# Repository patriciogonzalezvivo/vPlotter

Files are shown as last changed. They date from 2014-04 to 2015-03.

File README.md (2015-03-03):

### Basic principes 

The vPlotter is essentially a vertical drawing machine that consists of a marker suspended between two motors which moves it over a wall surface.

The math involved in the movement of the marker over the surface is extremely simple. It requires knowing the distance between the motors to calculate how much string distance each motor has to give to the marker (plotter head). This distance can be calculated using Pythagoras' theorem.

GRAPH

Both motors are attached to the wall at the same height to the floor separated by a given distance. The more distance there is between them, the larger the drawing area. I usually separate the motors by 1.5 meters (1500 mm). 

	distance_between_motors = 1500;

So the motors' positions can be represented as: 

	M1.x = 0;
	M1.y = 0;

	M2.x = M1.x + distance_between_motors;		// 1500
	M2.y = 0;

Knowing this we can calculate the position of the plotter head using Pythagoras' theorem. Imagine the triangles composed by the two motors and the plotter head as two right triangles. For each motor we need to find the distance (square root) to the marker. By releasing this amount of string to the plotter head, gravity will make the rest, by tensing the string.

	distance.M1 = square_root( M1.x*M1.x + M1.y*M1.y );
	distance.M2 = square_root( M2.x*M2.x + M2.y*M2.y );

To have precise control on the motors' movements, I'm using two [NEMA 17 steppers motors](https://ultimachine.com/content/kysan-1124090-nema-17-stepper-motor) controlled with a [Pololu A4988 Stepper Driver](https://ultimachine.com/content/pololu-a4988-stepper-driver-heatsink-kit) for each one. 

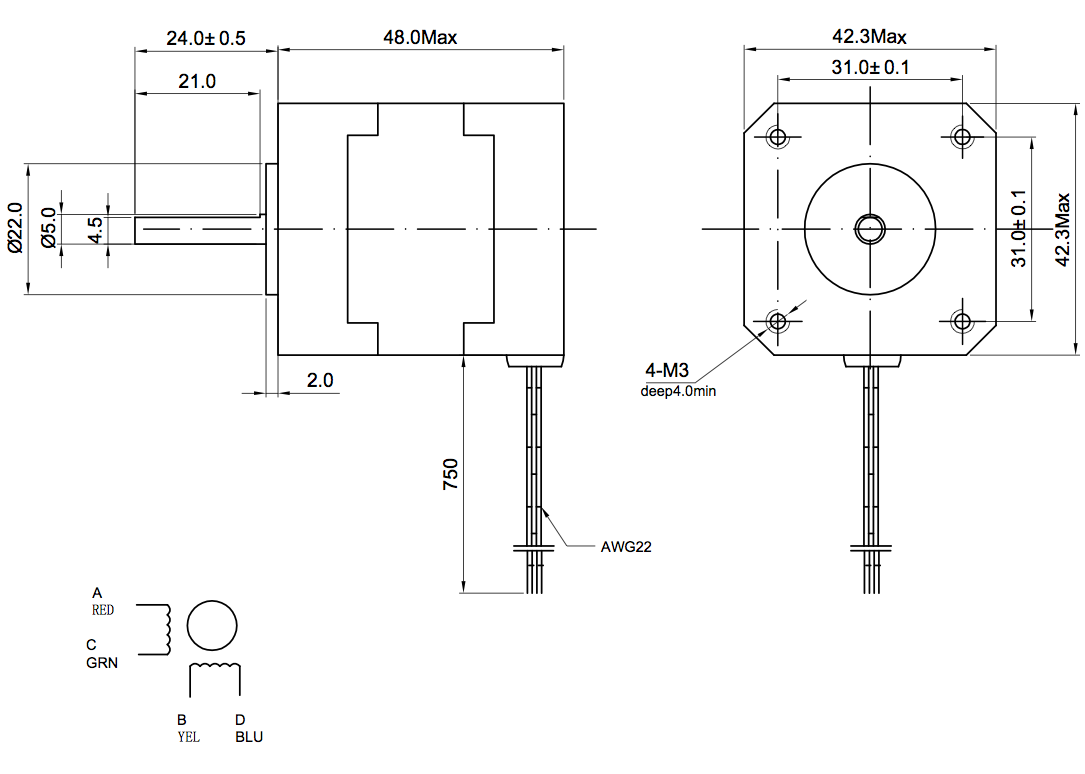
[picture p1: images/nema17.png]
nema17 (https://ultimachine.com/content/kysan-1124090-nema-17-stepper-motor)
 

Nema 17 motors have 200 steps for rotation but by enabling quarters of steps on the Pololu drivers we can obtain up to 800 steps for rotation which allows for much more precision. Next we need to calculate the circumference of the pulleys to determine how many millimeters we have for each step. In my case I'm using two [Timing Pulley GT2 of 20 tooth](https://ultimachine.com/content/timing-pulley-gt2-20-tooth) which have a bore of 5mm and match the [GT2 Timing Belt](https://ultimachine.com/content/timing-belt-gt2-custom-length) that holds the plotter header. From that we can calculate the amount of steps using these formulas:

	STEPS = 800;
	DIAMETER = 5; // 5mm
	CIRCUMFERENCE = DIAMETER * PI; // 15.7 mm
	m2s = CIRCUMFERENCE / STEPS; // 0.019625 mm for step

Keeping track of how much string each motor has moved we can estimate with a precision of 0.019625mm the position of the plotter head. I'm keeping track of the number of steps in a structured variable called MotorVal :

	struct MotorVal{
  	  long M1;
    	long M2;
	};

 To calculate the plotter drawing head we can use absolute parameters or relative. This means the an absolute position or a position relative to the previous one. In order to have accurate absolute positions is necessary to know the starting position of the plotting head. For that I use a physical mark on the center of the drawing area to manually adjust the plotter header at the beginning of each drawing work. Other drawing machines like laser cutters or CNC machines have sensors to estimate the initial position.

Another important feature of this drawing machine is the ability to start and stop drawing by moving the marker closer to or further from the wall surface. This is done using a [Micro Servo Motor](http://www.adafruit.com/products/169) mounted on the plotter head. Servos use frequency of pulse to calculate the angle of the motor. They can go from -90 to 90 deg (0 - 180 deg), alternating between 544 to 2400 pulses per second. By moving the marker towards or away from the surface, we can control when it is drawing lines and when it is just moving. This, together with the absolute or relative coordinates, defines 4 types of commands:

	enum Command{
  	  MOVE_ABS = 0,
    	MOVE_REL,
    	LINE_ABS,
    	LINE_REL
	};

Using these commands each line of a drawing is translated to instructions to the motors. 

	void vPlotter::print(vector<ofPolyline> _paths){
		for(int i = 0; i < _paths.size(); i++) {
			for(int j = 0; j < _paths[i].getVertices().size(); j++){
				addInstruction( ((j==0)?MOVE_ABS:LINE_ABS), _paths[i].getVertices()[j] );
			}
		}
		addInstruction(MOVE_ABS, printingArea.getCenter());
	}

	bool vPlotter::addInstruction(Command _command, ofPoint _pos){
		ofPoint t;

		//  ABSolute or RELative positions??
		//
		switch (_command) {
			case MOVE_ABS:
			case LINE_ABS:
				t = _pos;
				break;
			case MOVE_REL:
			case LINE_REL:
				t = _pos + currentPos;
				break;
		}

		//  Make instruction
		//
		Instruction inst;
		inst.set(_pos);
		inst.cmd = _command;
		inst.target = getStepsFor(_pos);

		//  Add
		//
		instructions.push_back(inst);
	}

	MotorVal vPlotter::getStepsFor(ofPoint _pos) {
		MotorVal val;
		val.M1 = M1.distance(_pos)/m2s;
		val.M2 = M2.distance(_pos)/m2s;
		return val;
	}

To ensure consistency, I'm adding an extra instruction that moves the head of the plotter to the center of the printing area. This prevents the user from having to manually move the head of the plotter to the physical mark on the center of the plotting area.

These instructions are then processed in another thread sending each motor the number of steps it has to move and in which direction. Controlling real motors means being constrained by real behavior - that means being aware of the physical stress (thermal and electrical) together with the time a task takes to be executed. This is the function that executes the instructions, that calculates the pauses and pulses to the motors. 

	void vPlotter::threadedFunction(){
		while( isThreadRunning() != 0 ){
			if (isPrinting()){
				if(getInstructionsLeft()){
					if (exeInstruction(instructions[0])){
						if(lock()){
							instructions.erase(instructions.begin());
							unlock();
						}
					}
				} else {
					bPlotting = false;
					stopThread();
				}
			}
		}
	}

	bool vPlotter::exeInstruction(Instruction _inst){
		MotorVal t, s;
		float sd,pd;

		//  Set the right PEN
		//
		sd = stepDelay*1000.0f;
		pd = penDelay*1000.0f;
		switch (_inst.cmd) {
			case LINE_REL:
			case LINE_ABS:{
				if(penState == PEN_UP){
					softServoWrite(SERVO_PIN,penPosDown);
					usleep(pd);
				}
				penState = PEN_DOWN;
				break;
			}
			case MOVE_REL:
			case MOVE_ABS:{
				if(penState == PEN_DOWN){
					softServoWrite(SERVO_PIN,penPosUp);
					usleep(pd);
				}
				penState = PEN_UP;
				break;
			}
		}

		// Tmp Variables
		t = target = _inst.target;
		s = steps;
    
		// set directions
		MotorVal dir;
		dir.M1 = (t.M1 > s.M1) ? +1 : -1;
		dir.M2 = (t.M2 > s.M2) ? +1 : -1;
		digitalWrite(DIR_PIN_M1, (t.M1 > s.M1) ? DIR_UP : DIR_DOWN);
		digitalWrite(DIR_PIN_M2, (t.M2 > s.M2) ? DIR_DOWN : DIR_UP);

		//  Make steps
		//
		while (s!=t){
			if( t.M1 - s.M1 != 0){
				digitalWrite(STEP_PIN_M1, HIGH);
				s.M1 += dir.M1;
			}

			if(t.M2-s.M2 != 0){
				digitalWrite(STEP_PIN_M2, HIGH);
				s.M2 += dir.M2;
			}

			steps = s;
			currentPos = getPosFor(s);
			usleep(250);
			digitalWrite(STEP_PIN_M1, LOW);
			digitalWrite(STEP_PIN_M2, LOW);
			usleep(250);
			usleep(sd);
		}
		return true;
	}

	//	Reverse kinematics
	//
	ofPoint vPlotter::getPosFor(MotorVal _steps) {
		float a = _steps.M2 * m2s;
		float b = _steps.M1 * m2s;
		float c = motorsDistance;
		return calcPointB(a, b, c);
	}

	ofPoint vPlotter::calcPointB(float a, float b, float c){
		double angle = acos((b*b+c*c-a*a)/(2*b*c));
		return ofPoint(b*cos(angle)+M1.x,b*sin(angle)+M1.y);
	}

These functions are the core operations behind the drawing. To make the vPlotter a proper tool I designed a reliable and flexible infrastructure based on openFrameworks (C++) and Node (JS) on top of a Linux OS running on a raspberryPi.

### Hardware

- 2 x [Nema 17 Stepper Motor](https://ultimachine.com/content/kysan-1124090-nema-17-stepper-motor)

- 2 x [Pololu A4988 Stepper Driver](https://ultimachine.com/content/pololu-a4988-stepper-driver-heatsink-kit)

- 2 x [Timing Pulley, GT2, 20 Tooth](https://ultimachine.com/content/timing-pulley-gt2-20-tooth)

- 6m of [Timing Belt, GT2, Custom Length](https://ultimachine.com/content/timing-belt-gt2-custom-length)

- 1 x [Micro Servo](http://www.adafruit.com/products/169) 

- 15x15 inch of Plywood 

- [Raspberry Pi](https://www.adafruit.com/products/998)

- [GPIO Ribbon Cable](https://www.adafruit.com/products/862)

- [Adafruit Half-size Perma-Proto](https://www.adafruit.com/products/1148)

- Optional [PiTFT](https://www.adafruit.com/products/1601) screen for visual debug

RaspberryPi is a small and cheap board capable of running a complete Linux system. The RaspberryPi has some General Input's and Outputs (GPIO) that will let us connect this board to the stepper motors' drivers (Pololu) and the mini servo motors.

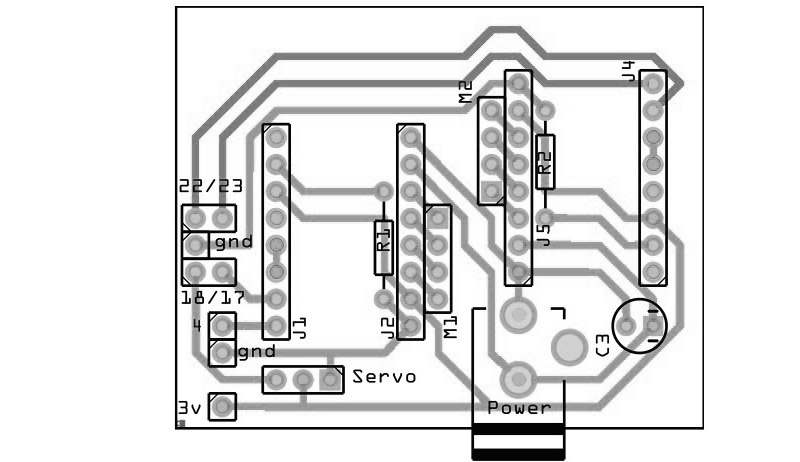
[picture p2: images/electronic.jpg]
Electronic Board


Because the servo uses frequency of pulses it will use the GPIO number 18 that has PWM capabilities. For the two motor drivers we use the GPIOs 4, 17, 23 and 22. Each driver will require both a _step_ and a _direction_ pulse to know when and how to make the rotation. These values can be modified at the top of the `vPlotter.h` file

	#define SERVO_PIN 18

	#define STEP_PIN_M1 4
	#define DIR_PIN_M1 17

	#define STEP_PIN_M2 23
	#define DIR_PIN_M2 22

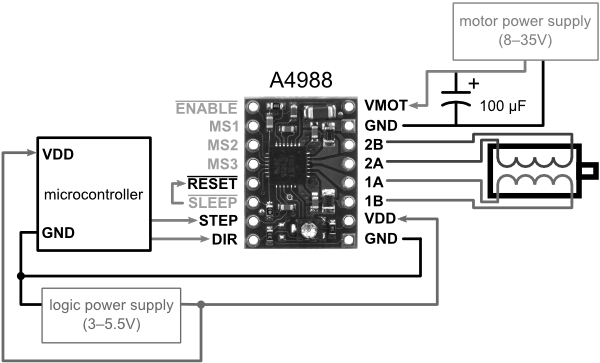
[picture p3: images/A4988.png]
A4988


### Software

The RaspberryPi uses a derived version of the Debian Linux distribution as its operating system. This software architecture is famous for it stability, security and modularity. Each new program installed onto the computer becomes part of a robust ecosystem of applications that can be re-combined in different ways.

In the case of the vPlotter the C++ code I wrote using openFrameworks constitutes the core application capable of being executed directly from the command line as follows:

	vPlotter -i file.svg

It is possible to modify some setup parameters like the distance between motors by doing:

	vPlotter -d 2000 -i file.svg

This application can print vector files (known as SVG format) and can also listen for instructions on a OSC port (for example the port 1010101).

	vPlotter -o 101010

Another feature of this application is the possibility of receiving visual feedback of the instructions on the pull by adding the option -x

	vPlotter -x -o 1010101
	vPlotter -x -i file.svg

It's possible to combine vPlotter with other tools using Unix pipe commands like this: 

	potrace -s image.png || vPlotter -i

In this case we are using the program ['potrace'](http://potrace.sourceforge.net/) to transform an image to vectors (-s) to then print it using vPlotter. Using similar techniques, it is possible to transform a picture of a document to text to then assign some style and fonts to then vectorize and finally print with the plotter. The combinations are infinite.

But not all users are comfortable running linux commands as part of their creative practice. That's why I design a Node.js server that provides an web API to administrate calls to the vPlotter. Users can ask for jobs in the plotter queue together with the setup parameters by making a call to `rpi.local:8080/status.json`. Using the same API users can `add` tasks to the queue or change the setting options of the vPlotter. A hypothetical user with intermediate knowledge of HTML/CSS/JS can use the plotter remotely by sending and receiving calls to this API.

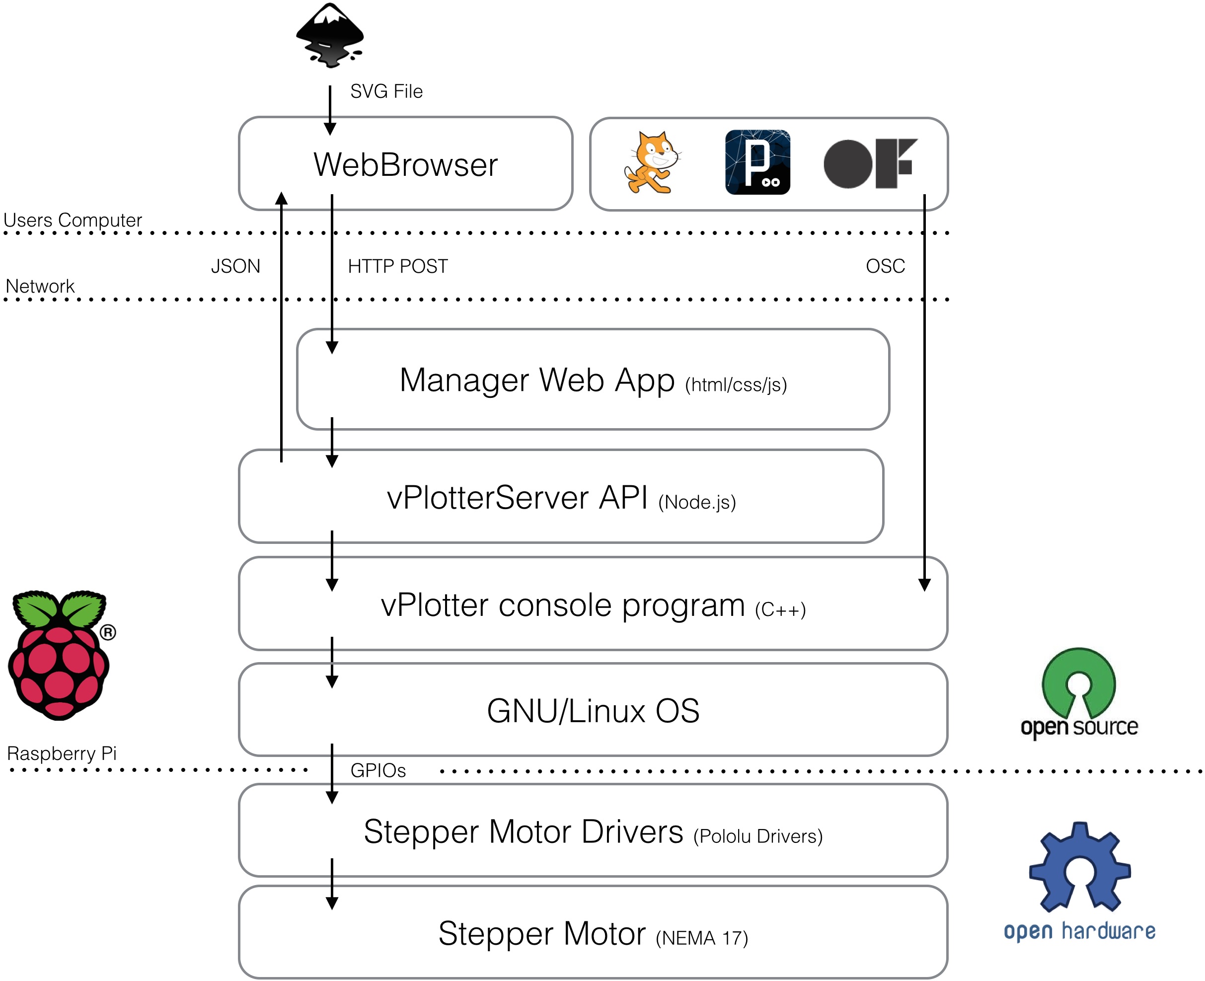
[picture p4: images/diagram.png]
Modular design of the vPlotter


It's possible that the user does not have the technical knowledge to use the API, which is why I have also incorporated on the server a web site from which it is possible to drag & drop files to the queue. I've designed a tool that can be access ed from a wide spectrum of architectural layers.

<iframe src="//player.vimeo.com/video/81298249?title=0&amp;byline=0&amp;portrait=0&amp;color=ffffff" width="574" height="323" frameborder="0" webkitallowfullscreen mozallowfullscreen allowfullscreen></iframe>

##### Software Installation

1. In order to compile and install the vPlotter binaries in the right place you will need to [install openFrameworks](http://openframeworks.cc/setup/raspberrypi/Raspberry-Pi-Getting-Started.html). For that please follow [this guide](http://openframeworks.cc/setup/raspberrypi/Raspberry-Pi-Getting-Started.html). Be prepared, it is going to take a while.

2. Once you have your openFrameworks installed and working (please check it by compiling some of the examples), clone this repository inside the `/home/pi/openframeworks/apps` folder.

~~~
	cd ~/openFrameworks/apps
	git clone https://github.com/patriciogonzalezvivo/vPlotter
~~~

5. The last step is to run the installation script which will install [Node.js](http://nodejs.org/) for the server, [WiringPi](https://projects.drogon.net/raspberry-pi/wiringpi/) to communicate through the GPIOs, compile `vPlotter` and install `vPlotterServer` as a local daemon.

~~~
	cd ~/openFrameworks/apps/vPlotter
	./install.sh
~~~

### Precedents & Research

Wall Plotter has been around for a while. My work is continuing what others have started. The first documented wall-plotter was develop by [Jurg Lehni]((http://juerglehni.com), and was called [Hektor](http://juerglehni.com/works/hektor/). Jurg is a fascinating artist committed to tool making, especially related to drawing.

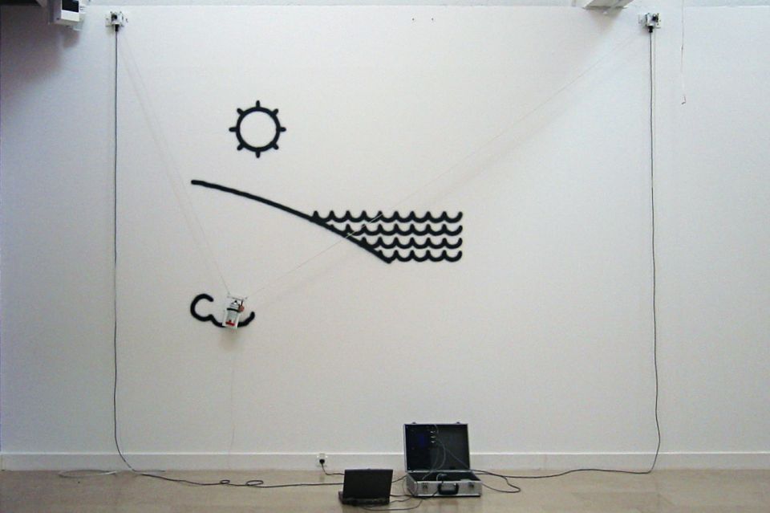
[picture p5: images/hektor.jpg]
Hektor by Jurg Lehni (http://juerglehni.com/works/hektor/)


In my case I start working based on [Alexander Weber's](http://tinkerlog.com/) wall plotter called [Kritzler](http://tinkerlog.com/2011/09/02/der-kritzler/). He's done amazing work documenting the process together with comprenhensible [code](https://github.com/tinkerlog/Kritzler). This version is designed to run with an Arduino plugged into a computer. My first effort on this project was porting the code to openFrameworks to then compile and run on the RaspberryPi, but the basic core logics behind the algorithmic kinematics are pretty much the same as what Alex wrote.

Kritzler by Alexander Weber (http://tinkerlog.com/2011/09/02/der-kritzler/)

Alexander documentation (http://tinkerlog.com/2011/09/02/der-kritzler/)

While I was experimenting with the Plotter I rapidly discovered how important it is to calculate the right printing area. The variations on the tensions on the strings that hold the plotter head are vital to obtain good results on the marker traces.

Doing some research I found some valuable documentation on [this website](http://2e5.com/plotter/V/design/) of how to obtain both resolution and tension coefficient. Since they are presented in Python I translated them into C++ and added to some methods and functions that calculate the best area given a specific distance between the motors.

Printing Area (http://2e5.com/plotter/V/design/)

The presence of mathematics concepts in drawings have a long history. The laws of perspective and proportions are one of the first technical tools we use. In my process of making a drawing machine I learned how to connect and work together with physics and mechanical principles. 

Sometimes drawing tools aren't born from a long history of techniques and apparatus. They are discovered as the repurpose of everyday machines. This is the case of the drawings made by [Echo Yang](http://www.junk-culture.com/2014/02/designer-transforms-old-school-analog.html#more).

Echo Yang's drawing machine (http://www.junk-culture.com/2014/02/designer-transforms-old-school-analog.html#more)

There are other examples of drawing machines, ones that formulate a question not about the tools but about the user. These are the cases of sophisticated robots armed with regular brushes and analog paint. These robots mimic our use of these tools in the search of becoming autonomous agents. [eDavid](http://www.informatik.uni-konstanz.de/en/edavid/news/) designed by Oliver Deussen and Thomas Lindemeier is an example of a machine that performs accurate drawings, while the robot designed by [Benjamin Grosser](http://bengrosser.com/projects/interactive-robotic-painting-machine/) explores some "expressive" visual representations of sound.

Ben Grosser Drawing Machine (http://bengrosser.com/projects/interactive-robotic-painting-machine/)

##### More references to drawing machines

- [Viktor](http://www.we-find-wildness.com/2011/01/juerg-lehni-viktor/)

- [Norwegian Creation's Drawing Machine](http://www.norwegiancreations.com/2012/04/drawing-machine-part-2/)

- [SADbot](http://www.instructables.com/id/SADbot-the-Seasonally-Affected-Drawing-robot/)

- [Harvey Moon's The Drawing Machine](http://www.unanything.com/Drawbot.html)

- <http://www.kickstarter.com/projects/notever/the-drawing-machine > <http://www.creativeapplications.net/maxmsp/drawing-machine-maxmsp-processing/>

- [Der Kritzler](http://tinkerlog.com/2011/09/02/der-kritzler/
Polargraph )

- <http://www.polargraph.co.uk>

- [Tristan Perich's Drawing Machine](http://tristanperich.com/Art/Machine_Drawings/)

- Paul Ferragut's Wall Drawing Machine: <http://vimeo.com/20526787> <http://vimeo.com/35647507> <http://vimeo.com/26900180>

- Douglas Irving Repetto's Giant Painting Machine:<http://music.columbia.edu/~douglas/portfolio/GPM_sanmateo_peoria_sf/> <http://music.columbia.edu/~douglas/portfolio/GPM_milano/>

- [Sprite Mod's White Board Plotter](http://spritesmods.com/?art=whiteboard&f=had)

- DrawBot:<http://www.marginallyclever.com/category/drawbot-my-creations/> <https://github.com/i-make-robots/DrawBot>
<http://web.me.com/sami6877/unanything/Site/Secret_Work/Entries/2010/6/1_Drawbot.html> <http://blog.makezine.com/2010/07/30/drawbot-takes-its-time-to-sketch/>

- [AS220 Lab's Drawbot](http://www.as220.org/labs/drawbot/instructions.html)

- [Make Magazine's Drawing Machine](http://makezine.com/makeitlast/) <http://makermedia.cmail4.com/t/ViewEmail/r/351C80A070878603/6423113868B805CEC9C291422E3DE149>
<http://blog.makezine.com/2011/02/24/make-it-last-build-3-rigging-up-your-drawbot/>

- [Muralizer](http://www.muralizer.com/blog/) <http://www.kickstarter.com/projects/1910641777/muralizer-it-prints-on-walls> <http://blog.makezine.com/2009/10/29/muralizer-prints-art-on-the-wall/> 

- [InternBot](http://jamesprovost.com/blog/introducing-internbot/)

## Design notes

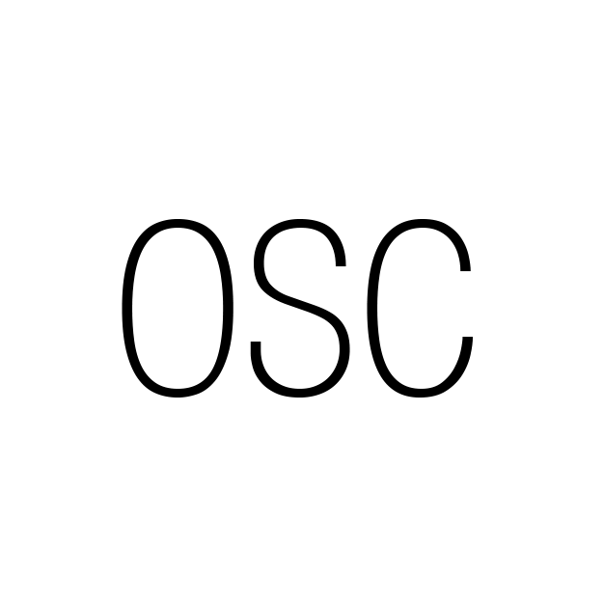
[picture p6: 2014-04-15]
vPlotterServer/www/images/osc.png

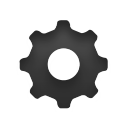
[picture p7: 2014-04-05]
vPlotterServer/www/images/gear.png

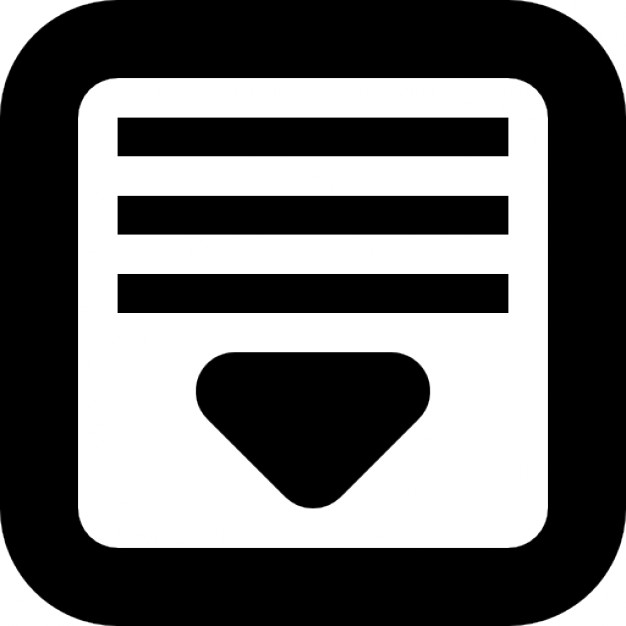
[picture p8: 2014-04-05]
vPlotterServer/www/images/main.jpg

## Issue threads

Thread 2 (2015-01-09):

Erroe while trying to Make vPlotter

LangBalthazar, 2015-01-09:
Hi,

Your project seems great! And I would very much like to try your setup.

But when i try to make according to your installation guide it fails as below on:
```
fatal error: ofxPiTFT.h: Filen eller katalogen finns inte
compilation terminated.
```
translated to ofxPiTFT.h is missing.

It is included online 6 and 27 in vPlotter/vPlotter/src/ofApp.h
If i comment out both refs to ofxPiTFT in ofApp.h it makes (with only warnings on other things)

The full make process below:
```
pi@drinkpi ~/openFrameworks/apps/vPlotter/vPlotter $ make
armv6l
checking pkg-config libraries:   cairo zlib gstreamer-app-1.0 gstreamer-1.0 gstreamer-video-1.0 gstreamer-base-1.0 libudev freetype2 fontconfig sndfile openal openssl libpulse-simple alsa gtk+-2.0 libmpg123
Compiling OF library for Release
armv6l
checking pkg-config libraries:   cairo zlib gstreamer-app-1.0 gstreamer-1.0 gstreamer-video-1.0 gstreamer-base-1.0 libudev freetype2 fontconfig sndfile openal openssl libpulse-simple alsa gtk+-2.0 libmpg123
make[1]: Entering directory `/home/pi/openFrameworks/libs/openFrameworksCompiled/project'
armv6l
checking pkg-config libraries:   cairo zlib gstreamer-app-1.0 gstreamer-1.0 gstreamer-video-1.0 gstreamer-base-1.0 libudev freetype2 fontconfig sndfile openal openssl libpulse-simple alsa gtk+-2.0 libmpg123
make[2]: Inget behöver göras för "ReleaseABI".
armv6l
checking pkg-config libraries:   cairo zlib gstreamer-app-1.0 gstreamer-1.0 gstreamer-video-1.0 gstreamer-base-1.0 libudev freetype2 fontconfig sndfile openal openssl libpulse-simple alsa gtk+-2.0 libmpg123
Done!
make[1]: Leaving directory `/home/pi/openFrameworks/libs/openFrameworksCompiled/project'

Compiling vPlotter for Release
armv6l
checking pkg-config libraries:   cairo zlib gstreamer-app-1.0 gstreamer-1.0 gstreamer-video-1.0 gstreamer-base-1.0 libudev freetype2 fontconfig sndfile openal openssl libpulse-simple alsa gtk+-2.0 libmpg123
make[1]: Entering directory `/home/pi/openFrameworks/apps/vPlotter/vPlotter'
../../../libs/openFrameworksCompiled/project/makefileCommon/config.project.mk:179: The following unknown addons will be ignored:
../../../libs/openFrameworksCompiled/project/makefileCommon/config.project.mk:180: ofxPiTFT
Compiling src/main.cpp
g++ -c -O3 -Wall -march=armv6 -mfpu=vfp -mfloat-abi=hard -fPIC -ftree-vectorize -Wno-psabi -pipe -DOF_USING_GTK -DOF_USING_MPG123 -DTARGET_RASPBERRY_PI -DSTANDALONE -DPIC -D_REENTRANT -D_LARGEFILE64_SOURCE -D_FILE_OFFSET_BITS=64 -D_FORTIFY_SOURCE -D__STDC_CONSTANT_MACROS -D__STDC_LIMIT_MACROS -DTARGET_POSIX -DHAVE_LIBOPENMAX=2 -DOMX -DOMX_SKIP64BIT -DUSE_EXTERNAL_OMX -DHAVE_LIBBCM_HOST -DUSE_EXTERNAL_LIBBCM_HOST -DUSE_VCHIQ_ARM -DUSE_DISPMANX_TRANSFORM_T -I./addons/ofxWiringPi/libs/wiringPi/include -I./vPlotter.xcodeproj/xcshareddata -I./vPlotter.xcodeproj/xcshareddata/xcschemes -I./src -I./addons -I./addons/ofxWiringPi -I./addons/ofxWiringPi/libs -I./addons/ofxWiringPi/libs/wiringPi -I./addons/ofxWiringPi/libs/wiringPi/libs -I./addons/ofxWiringPi/libs/wiringPi/include -I../../../addons/ofxOsc/src -I../../../addons/ofxOsc/libs -I../../../addons/ofxOsc/libs/oscpack -I../../../addons/ofxOsc/libs/oscpack/src -I../../../addons/ofxOsc/libs/oscpack/src/osc -I../../../addons/ofxOsc/libs/oscpack/src/ip -I../../../addons/ofxOsc/libs/oscpack/src/ip/posix -I../../../addons/ofxOsc/libs/oscpack/src/ip/win32 -I../../../addons/ofxSvg/src -I../../../addons/ofxSvg/libs -I../../../addons/ofxSvg/libs/svgTiny -I../../../addons/ofxSvg/libs/svgTiny/src -I/opt/vc/include -I/opt/vc/include/IL -I/opt/vc/include/interface/vcos/pthreads -I/opt/vc/include/interface/vmcs_host/linux -pthread -D_REENTRANT -I/usr/include/cairo -I/usr/include/glib-2.0 -I/usr/lib/arm-linux-gnueabihf/glib-2.0/include -I/usr/include/pixman-1 -I/usr/include/freetype2 -I/usr/include/libpng12 -I/usr/include/gstreamer-1.0 -I/usr/include/alsa -I/usr/include/gtk-2.0 -I/usr/lib/arm-linux-gnueabihf/gtk-2.0/include -I/usr/include/atk-1.0 -I/usr/include/gdk-pixbuf-2.0 -I/usr/include/pango-1.0 -I/usr/include/gio-unix-2.0/ -I/usr/include/harfbuzz -I../../../libs/fmodex/include -I../../../libs/glfw/include -I../../../libs/glfw/include/GLFW -I../../../libs/kiss/include -I../../../libs/openssl/include -I../../../libs/openssl/include/openssl -I../../../libs/poco/include -I../../../libs/rtAudio/include -I../../../libs/tess2/include -I../../../libs/openFrameworks -I../../../libs/openFrameworks/events -I../../../libs/openFrameworks/app -I../../../libs/openFrameworks/graphics -I../../../libs/openFrameworks/video -I../../../libs/openFrameworks/sound -I../../../libs/openFrameworks/types -I../../../libs/openFrameworks/gl -I../../../libs/openFrameworks/communication -I../../../libs/openFrameworks/utils -I../../../libs/openFrameworks/3d -I../../../libs/openFrameworks/math  -MMD -MP -MF obj/linuxarmv6l/Release/src/main.d -MT obj/linuxarmv6l/Release/src/main.o -o obj/linuxarmv6l/Release/src/main.o -c src/main.cpp
In file included from src/main.cpp:3:0:
src/ofApp.h:6:22: fatal error: ofxPiTFT.h: Filen eller katalogen finns inte
compilation terminated.
make[1]: *** [obj/linuxarmv6l/Release/src/main.o] Fel 1
make[1]: Leaving directory `/home/pi/openFrameworks/apps/vPlotter/vPlotter'
make: *** [Release] Fel 2
pi@drinkpi ~/openFrameworks/apps/vPlotter/vPlotter $
```

patriciogonzalezvivo, 2015-01-09:
Sorry, I forget to add a line on the documentation to clone the addon [ofxPiTFT](https://github.com/patriciogonzalezvivo/ofxPiTFT)

Closed 2015-01-09.

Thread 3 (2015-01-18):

Servo gitter

LangBalthazar, 2015-01-18:
Thank you for all your work. I have a question related to the servo.

I have everything wired up and workin on my desk but the servi is very jumpy.

It has the power to lift my heavy gondola with two 6005 bearings but it is jumping all the time
See example here:
http://www.youtube.com/watch?v=vTT_pI-Varo

I sit just me or is the normal behavior?

If I putty in and do a mode switch to pwm the servo is silent and then sudo gpio pwm 1 122 it moves and then silent.
Once I export the port again as done in the file in vplotterserver it starts to jump and make noise as in the video.

Is this Normal or do you any hints on how to improve this?

LangBalthazar, 2015-01-18:
In the video I have the servo connected to gpio18 / wiringpi gpio1, 3.3v and gnd on the pi The idle movements and noise is much louder when running servo + on 5v from the pi

patriciogonzalezvivo, 2015-01-23:
Hi @LangBalthazar ! yes I was having similar behavior. but stops once the GPIO library was load with the program. That's probably because of the noise on the GPIOs and the way servos works. There should be a way to fix it with proper wiring, but I don't know how to do it yet. Let me know if you find any tip. Thanks

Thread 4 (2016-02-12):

lines = p.getOutline  initialization of reference of type error

elid, 2016-02-12:
Hi Patricio,
First Thanks for your amazing work on the vPlotter :)
I had to correct the line 29 on ofApp.cpp file to compile the app correctly
from
vector<ofPolyline>& lines = p.getOutline();
to
vector<ofPolyline>& lines = const_cast<vector<ofPolyline>&>(p.getOutline());
apparently p.getOutline need to cast as a polyline array on raspberry pi

Since I'm quite new to oF and to c++, I could not figure out how to use your UI version yet,
but I'll dig a bit deeper and will surely find out.

Thanks!
/Frederic

sobrien556, 2019-03-26:
Hi Frederic, I am still receiving an error upon compilation, even with your suggestions. I have attached the screenshot of the errors I recieved. Thanks!
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
(url)

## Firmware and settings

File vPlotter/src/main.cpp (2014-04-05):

#include "ofMain.h"

#include "ofApp.h"
#include "ofAppNoWindow.h"

#include <algorithm>

char* getCmdOption(char ** begin, char ** end, const std::string & option){
    char ** itr = std::find(begin, end, option);
    if (itr != end && ++itr != end)
    {
        return *itr;
    }
    return 0;
}

bool cmdOptionExists(char** begin, char** end, const std::string& option){
    return std::find(begin, end, option) != end;
}

void printVersion(){
    cout << "vPlotter 0.1" << endl;
    cout << "Copyright (c) 2013 Patricio Gonzalez Vivo ( http://www.patriciogonzalezvivo.com )" << endl;
    cout << "This is free software with ABSOLUTELY NO WARRANTY." << endl;
}

//========================================================================
int main(int argc, char * argv[]){
    
    //  SYSTEM
    //----------------------------------------------
    //
#ifdef TARGET_RASPBERRY_PI
    bool noWindows = true;
    if(cmdOptionExists(argv, argv+argc, "-x")){
        noWindows = false;
    }
#else
    bool noWindows = false;
#endif
    ofAppNoWindow noWindowApp;
    if(noWindows){
        ofSetupOpenGL(&noWindowApp, 1024,768, OF_WINDOW);
    } else {
        ofSetupOpenGL(1024,768, OF_WINDOW);
    }
    
    ofApp *app = new ofApp();
    app->sysGpio = true;
    app->bFit = true;
    app->file = "tux.svg";
    app->scale = 100;
    app->rotate = 0;
    app->mmMotorsDistance = 1500;
    app->mmPulleyRadius = 5;
    app->stepsPerRotation = 800;
    app->stepDelay = 1;
    app->degPenUp = 140;
    app->degPenDown = 70;
    app->penDelay = 2000;
    app->oscPort = -1;
    
    if(cmdOptionExists(argv, argv+argc, "-gipo")){
        app->sysGpio = false;
    }
    
    //  HELP
    //
    if(cmdOptionExists(argv, argv+argc, "-v")){
        printVersion();
        return 0;
    }
    
    if(cmdOptionExists(argv, argv+argc, "-h")){
        printVersion();
        cout << endl;
        cout << "Usage: vPlotter [options] -i file.svg" << endl;
        cout << endl;
        cout << "Options:" << endl;
        cout << "   -s [0-100]  Scale the image. Default: " << app->scale << endl;
        cout << "   -r [deg]    Rotate the image. Default: " << app->rotate << endl;
        cout << "   -nf         Don't fit." << endl;
        cout << "   -d [mm]     Distance between motors in mm. Default: " << app->mmMotorsDistance << endl;
        cout << "   -pr [mm]    Pulley Radius in mm. Default: " << app->mmPulleyRadius << endl;
        cout << "   -spr [stp]  Steps per Rotation. Default: " << app->stepsPerRotation << endl;
        cout << "   -sd [ms]    Step Delay. Default: " << app->stepDelay << endl;
        cout << "   -pu [deg]   Pen Up Angle. Default: " << app->degPenUp << endl;
        cout << "   -pd [deg]   Pen Down Angle. Default: " << app->degPenDown << endl;
        cout << "   -delay [ms] Pen Delay. Default: " << app->penDelay << endl;
        cout << "   -gipo       Direct GPIO connection. Not throught /dev/ files. Require Root priviledge" << endl;
        cout << "   -x          X Debug Windows. Default: "<< noWindows << endl;
        cout << "   -o [port]   Stream mode to OSC Port" << endl;
        return 0;
    }
    
    //  INPUT SVG file
    //
    char * filename = getCmdOption(argv, argv+argc, "-i");
    char * oscPort = getCmdOption(argv, argv+argc, "-o");

    if (filename){
        app->file = filename;
    }
    else if(oscPort){
        app->oscPort = ofToInt(oscPort);
    }
#ifdef TARGET_RASPBERRY_PI
    else {
        cout << "Usage: vPlotter [options] -i file.svg" << endl;
        return 0;
    }
#endif
    
    if(cmdOptionExists(argv, argv+argc, "-nf")){
        app->bFit = false;
    }
    
    char * scale = getCmdOption(argv, argv+argc, "-s");
    if(scale){
        app->scale = ofToFloat(scale);
    }
    
    char * rotate = getCmdOption(argv, argv+argc, "-r");
    if(rotate){
        app->rotate = ofToFloat(rotate);
    }
    
    //  MOTORS
    //
    char * d = getCmdOption(argv, argv+argc, "-d");
    if(d){
        app->mmMotorsDistance = ofToInt(d);
    }
    
    char * pr = getCmdOption(argv, argv+argc, "-pr");
    if(pr){
        app->mmPulleyRadius = ofToInt(pr);
    }

    char * spr = getCmdOption(argv, argv+argc, "-spr");
    if(spr){
        app->stepsPerRotation = ofToInt(spr);
    }
    
    char * sd = getCmdOption(argv, argv+argc, "-sd");
    if(sd){
        app->stepDelay = ofToFloat(sd);
    }
    
    //  PEN
    //
    char * pu = getCmdOption(argv, argv+argc, "-pu");
    if(pu){
        app->degPenUp = ofToInt(pu);
    }
    
    char * pd = getCmdOption(argv, argv+argc, "-pd");
    if(pd){
        app->degPenDown = ofToInt(pd);
    }
    
    char * pdelay = getCmdOption(argv, argv+argc, "-delay");
    if(pdelay){
        app->penDelay = ofToFloat(pdelay);
    }

    ofRunApp( app );
}

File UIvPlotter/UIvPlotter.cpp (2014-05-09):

//
//  UIvPlotter.cpp
//  09 - TraceMaker
//
//  Created by Patricio Gonzalez Vivo on 10/9/13.
//
//

#include "UIvPlotter.h"

UIvPlotter::UIvPlotter(){
    motorsDistance      = 500;//1549;
    pulleyRadius        = 5;
    stepsPerRotation    = 800;
    
    host                = "192.168.1.12";
    oscPort             = 101010;

    currentPos.set(0,0);
    
    steps.M1    = 0;
    steps.M2    = 0;
    
    target.M1   = 0;
    target.M2   = 0;
    
    penState    = PEN_UP;
    bPlotting   = false;
    
    checkHostValues();
    sender.setup(host, oscPort);
    
//    textField = NULL;
}

void UIvPlotter::setupUI(){
//    textField = gui->addTextInput("HOST", "", OFX_UI_FONT_SMALL);
    
    gui->addLabel("Config");
    gui->addIntSlider("motorsDistance_(mm)", 0, 2000, &motorsDistance);
    gui->addIntSlider("pulleyRadius_(mm)", 0, 50, &pulleyRadius);
    gui->addIntSlider("stepsPerRotation", 0, 1000, &stepsPerRotation);
    gui->addIntSlider("penUp_(deg)", 0, 180, &penUp);
    gui->addIntSlider("penDown_(deg)", 0, 180, &penDown);
    bool bFalse = false;
    gui->addButton("SYNC", bFalse);
    
    gui->addButton("CLOSE", bFalse);
}

void UIvPlotter::guiEvent(ofxUIEventArgs &e){
    string name = e.widget->getName();
    
    if (name == "HOST"){
//        host = textField->getTextString();
        checkHostValues();
    } else if(name == "SYNC"){
        checkHostValues();
    } else if(name == "CLOSE"){
        ofxOscMessage m;
        m.setAddress("/stop");
        sender.sendMessage(m);
    } else {
        bUpdate = true;
    }
}

bool UIvPlotter::checkHostValues(){
    ofxJSONElement  response;
    
    std::string url = "http://"+host+":8080/status.json";
    
	if (!response.open(url)){
        cout  << "Failed to parse JSON\n" << endl;
    }
    
    penUp = ofToInt(response["options"]["penUpAngle"].asString());
    penDown = ofToInt(response["options"]["penDownAngle"].asString());
    motorsDistance = ofToInt(response["options"]["motorsDistance"].asString());
    pulleyRadius = ofToInt(response["options"]["pulleyRadius"].asString());
    stepsPerRotation = ofToInt(response["options"]["stepsPerRotation"].asString());
    
    bUpdate = true;
}

bool UIvPlotter::isHealthyAt(ofPoint _pos){
    ofVec2f tension = getTension(_pos);
    ofVec2f resolution = getResolution(_pos);
    if(tension.x<0||tension.y<0||
       tension.x>=0.8||tension.y>=0.8||
       resolution.x>=0.8||resolution.y>=0.8){
        return false;
    } else {
        return true;
    }
}

MotorVal UIvPlotter::getStepsFor(const ofPoint &_pos)const{
    MotorVal rta;
    rta.M1 = M1.distance(_pos)/m2s;
    rta.M2 = M2.distance(_pos)/m2s;
    return rta;
}

ofPoint UIvPlotter::getPosFor(const MotorVal &_steps)const{
    ofPoint rta;
    float a = _steps.M2 * m2s;
    float b = _steps.M1 * m2s;
    float c = motorsDistance;
    return calcPointB(a, b, c);
}

ofVec2f UIvPlotter::getTension(ofPoint _pos){
    float angleToM1 = atan2(_pos.y-M1.y,_pos.x-M1.x);
    float angleToM2 = atan2(_pos.y-M2.y,M2.x-_pos.x);
    float d = cos(angleToM1)*sin(angleToM2)+sin(angleToM1)*cos(angleToM2);
    float tensionToM1 = cos(angleToM2)/d;
    float tensionToM2 = cos(angleToM1)/d;
    return ofVec2f(tensionToM1,tensionToM2)-ofVec2f(0.5,0.5);
}

ofPoint UIvPlotter::calcPointB(float a, float b, float c)const{
    // law of cosines
    // http://en.wikipedia.org/wiki/Solution_of_triangles
    float angle = acos((b*b+c*c-a*a)/(2*b*c));
    return ofPoint(b*cos(angle)+M1.x,b*sin(angle)+M1.y);
}

ofVec2f UIvPlotter::getResolution(ofPoint _pos){
    ofVec2f rta;
    
    float c = M1.distance(M2);
    float b = M1.distance(_pos);
    float a = M2.distance(_pos);
    
    float err = .00000000001;
    ofPoint pc = calcPointB(a, b, c);
    if((_pos.x-err<pc.x<_pos.x+err) ||
       (_pos.y-err<pc.y<_pos.y+err)){
        float db = _pos.distance(calcPointB(a, b+1, c));
        float da = _pos.distance(calcPointB(a+1, b, c));
        return ofVec2f(da/1.4,db/1.4);
    }else{
        return ofVec2f(2,2);
    }
}

void UIvPlotter::print(ofPolyline _polyline){
    if(_polyline.size()>1){
        addInstruction(MOVE_ABS, _polyline.getVertices()[0]+ printingArea.getTopLeft());
        addInstruction(MOVE_ABS, _polyline.getVertices()[1]+ printingArea.getTopLeft());
    }
    
    for(int j = 0; j < _polyline.getVertices().size(); j++) {
        addInstruction(((j==0)?MOVE_ABS:LINE_ABS), _polyline.getVertices()[j] + printingArea.getTopLeft());
    }
    
    if (instructions.size() > 0) {
        addInstruction(MOVE_ABS, printingArea.getCenter());
        bPlotting = true;
    }
}

void UIvPlotter::print( vector<ofPolyline> _paths ){
    
    for(int i = 0; i < _paths.size(); i++) {
        if(_paths[i].size()>1){
            addInstruction(MOVE_ABS, _paths[i].getVertices()[0]+ printingArea.getTopLeft());
        }
        for(int j = 0; j < _paths[i].getVertices().size(); j++) {
            addInstruction( ((j==0)?MOVE_ABS:LINE_ABS), _paths[i].getVertices()[j] + printingArea.getTopLeft());
        }
    }
    
    if (instructions.size() > 0) {
        addInstruction(MOVE_ABS, printingArea.getCenter());
        bPlotting = true;
    }
}

bool UIvPlotter::addInstruction(Comand _command, ofPoint _pos){
    //  Make instruction
    //
    Instruction inst;
    inst.set(_pos);
    inst.cmd = _command;
    inst.target = getStepsFor(_pos);
    
    //  Add
    //
    instructions.push_back(inst);
}
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

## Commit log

2014-04-14 API > node.js
    TODO: use mongodb
    [config.csv, config.txt]
2014-04-14 printFirstOnLine at end
2014-04-27 better readme
    [vPlotter.fzz]
